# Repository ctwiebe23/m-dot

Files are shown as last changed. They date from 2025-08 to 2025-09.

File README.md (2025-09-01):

# Robot Car Project: M-DOT

Repo containing code and diagrams for a maze-navigating robot car built for my
Embedded Systems class.  The project uses an Arduino UNO, but operates purely
using the ATmega328P registers — no Arduino libraries.

## Directories

`./src`
: Contains C++ header and source files, as well as an executable program.  All
public function prototypes and macro definitions are in `mdot.hpp`, while all
implementations are split into their own `.cpp` files.  An example program
can be found in `src.ino`

`./doc`
: Contains documentation for the design of the project, such as wiring
diagrams and a report.

`./dat`
: Contains additional data, such as relevant datasheets and schematics.

## How to use M-DOT

M-DOT is a simple robot consisting of

- an Arduino UNO;
- an HC-SR04 ultrasonic sensor mounted on a servo;
- two DC motors connected to a L298N motor driver; and
- an IR receiver.

It can be controlled using the library found within this project, `mdot.hpp`.
This library consists of two types of functions:  Setup functions, and loop
functions.

The program entry point should be a `.ino` file that includes the M-DOT library
and contains a `setup()` function (ran once) along with a `loop()` function
(ran continuously).

```cpp
#include "mdot.hpp"

void setup(void) {
  configMDot();
  setDrift(0.95);
}

void loop(void) {
  Millimeters distance = getSonarDistance();

  if (distance < 40) {
    stop();
  } else {
    drive(100);
  }

  wait(100);
}
```

### Setup

The setup functions are intended to be used within the `setup()` Arduino
function.  They mostly follow the naming pattern `configFoo()` and are used to
configure each component, e.g. `configSonar()`, `configServo()`. For
convenience, a helper function `configMDot()` is provided that calls all other
configure functions.

Other setup functions include:

`void setDrift(float drift)`
: This function is used to handle drift in the drive (DC) motors.  It takes one
argument:  A float that represents the ratio of left motor power to right motor
power.  For instance, if M-DOT drifts to the right you might do:

```cpp
void setup(void) {
  configMDot();
  // M-DOT drifts right -> correct w/ motor ratio 90 : 100
  // 90 / 100 = 0.9
  setDrift(0.9);

  drive(100);
}

void loop(void) { }
```

### Main loop

The loop functions are intended to be used within the `loop()` Arduino
function, but are frequently used within `setup()` too.  They are what tells
M-DOT to execute various actions.  Most components only have one loop function.

`void curve(Percent leftPower, Percent rightPower)`
: Sets the speed and direction of each drive motor individually.

`void brake(void)`
: Brakes both motors, i.e. immediate stop.

`void drive(Percent power)`
: Expands to `curve(power, power)`.

`void pivot(Percent power)`
: Expands to `curve(power, -power)`.

`void stop(void)`
: Expands to `curve(0, 0)`.  Glide stop.

`void moveServoTo(Degrees angle)`
: Alters the servo angle.  Uses the range [-90, 90].

`Millimeters getSonarDistance(void)`
: Reads distance using the ultrasonic sensor.

`void wait(Milliseconds period)`
: Pause program execution.

`void startStopwatch(void)`
: Starts (or restarts) the stopwatch.

`Milliseconds getStopwatchTime(void)`
: Gets the current stopwatch time.

`ButtonPress getButtonPress(void)`
: Gets a button press from the IR receiver.

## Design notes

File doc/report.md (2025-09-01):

---
title: M-DOT
subtitle: Embedded Systems // Project Report
author: C Wiebe
date: May 9, 2025
numbersections: true
colorlinks: true
links-as-notes: true
toc: true
header:
  right: University of Placename
toc-on-own-page: true
margin-top: 1.2in
margin-bottom: 1.2in
margin-left: 1.2in
margin-right: 1.2in
fontfamily: tgschola
fontsize: 11pt
---

# Introduction

M-DOT is a Arduino-based maze-navigating robot car programmed using ATmega328P
registers and a custom library.  It uses two DC motors controlled by a L298
motor driver to maneuver, along with an HC-SR04 ultrasonic sensor mounted to a
SG90 servo to "see" its surroundings.  The goal of the project is to create a
robot car that can successfully navigate a maze-like obstacle course using its
onboard sensor.

Additionally, M-DOT can be controlled remotely using an AX-1838HS IR receiver
and Elegoo controller. This functionality is *not* used in maze navigation ---
that is totally autonomous.

# Preliminary Design

The robot has four main external components that need to be configured: The
servo, the sonar (ultrasonic sensor), the drivetrain (DC motors), and the (IR)
receiver.  They are
connected to the Arduino UNO as seen in Figure \ref{initial}

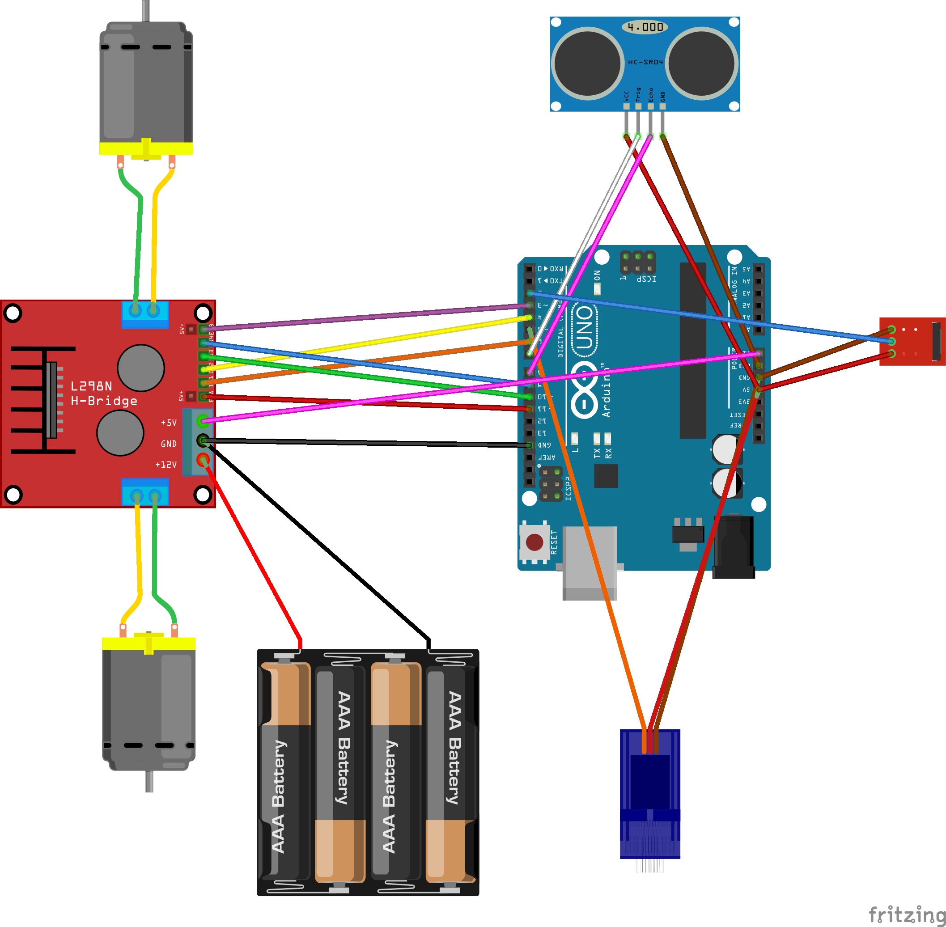
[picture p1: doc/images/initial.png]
Initial design schematic. \label{initial}


All three timers are used in configuring these components, as seen in Table
\ref{timers}.

: Timer configurations. \label{timers}

| Timer | Purpose | Mode | Output(s) |
| --- | --- | --- | --- |
| `timer0` | Servo PWM | Phase correct PWM | `OC0B` |
| `timer1` | General timer  | Normal | None |
| `timer2` | Drivetrain PWM | Phase correct PWM | `OC2A`, `OC2B` |

## Servo Configuration

In order to generate a PWM with the duty cycle and period expected by the SG90
servo, `timer0` was configured to use `OCR0A` as its TOP, the value of which
can be found with equation:
$$ \mathrm{TOP} = \mathrm{OCR0A} = \frac{\mathrm{CPU~frequency} \times
\mathrm{servo~period}}{\mathrm{prescaler} \times 2} = 156.25 \approx 156 $$
where:
\begin{alignat*}{3}
\mathrm{CPU~frequency} &= 16 \u{MHz} \\
\mathrm{servo~period} &= 20 \u{ms} \\
\mathrm{prescaler} &= 1024
\end{alignat*}

Since `OCR0A` is being used as TOP, the PWM is generated on `OC0B`.

## General Timer Configuration

General timer functions --- such as those needed by the sonar --- are provided
by `timer1`.  To this end, the timer is configured in normal mode with no major
modifications.  The timer does, however, make use of two interrupts:

1.  The timer overflow interrupt, `TOV1`, which will be used to increment a
    counter and track large spans of time.
2.  The output compare A interrupt, `OCIE1A`, which will be used by the
    receiver to determine when a data packet "times out".

## Sonar Configuration

The sonar uses two non-PWM pins --- one output (trigger) and one input (echo)
--- along with basic timer functions to measure signal lengths.

A reading begins by sending a ten microsecond pulse to the trigger.  The
duration of the return signal recieved on echo is then measured and used to
calculate the distance, using the equation:
$$ \mathrm{distance} \u{cm} = \mathrm{echo~duration}\u{\mu s} \times
\frac{\mathrm{centimeters}}{\mathrm{microsecond}} $$
where:
$$ \frac{\mathrm{centimeters}}{\mathrm{microsecond}} = 58 $$
Readings should be taken at least 60 milliseconds apart to prevent noise from
interfering with the measurement.

## Drivetrain Configuration

Each drivetrain motor is hooked into the L298 motor driver with two pins. The
Arduino itself is connected to the L298 using a three-wire interface (three
pins per motor):

- One wire is a PWM that connects to the motor enable pin and controls the
  "power" of the motor.
- The other two (non-PWM) wires control the direction of the motor.  When one
  pin is HIGH and the other LOW, the motor spins one way; swap which pin is
  HIGH and which is LOW to spin the motor the other way.  Set both pins equal
  to each other to "brake" the motor.

`timer2` is used to generate the PWM signals needed for both motor enable
wires.  These are generated on pins `OC2A` and `OC2B`.

## Receiver Configuration

The IR receiver will be hooked up to an external interrupt (which is idle HIGH)
so as to prevent the need for constant polling.  It will use `timer1` as a
pseudo watchdog timer by enabling and disabling an output compare match
interrupt.

The following process is used to receive data, which it stores in a
global "data packet":

1.  The external interrupt ISR is configured to fire on the falling edge,
    but that trigger will toggle between falling and rising edges each time it
    is called.
2.  When a falling edge interrupt fires, the current timer count is stored in
    the data packet and the watchdog timer is disabled, if it isn't already.
3.  When the rising edge interrupt fires, the timer count is cleared and the
    watchdog timer is started.  If the watchdog timer terminates, the data
    packet is marked as complete and the process is reset.

Each data packet sent will begin with a start bit, followed by 32 data bits,
and terminating with an end bit.  Each bit will consist of a "low half-bit" and
a "high half-bit".  The low half of the data bits is used to separate the high
halves, which will contain the actual data:  A long time spent high is a
logical 1, and a short time high is a logical 0.  The time spent low is
funtionally irrevelent.  Recorded times for the various half-bits can be seen
in Table \ref{lengths}.

: Recorded half-bit lengths.
\label{lengths}

| Type | Time [ms] |
| --- | ---: |
| Start low | 9.336 |
| Start high  | 4.456 |
| Data X low  | 0.644 |
| Data 0 high | 0.504 |
| Data 1 high | 1.592 |
| Stop low | 0.656 |
| Stop high | 39.992 |

In order to properly identify 1's and 0's in the data segement, additional
analysis was conducted, as seen in Table \ref{stats}.  The valid range
displayed in the table is the range that will correctly identify 99.9999426697%
of pulses (plus or minus five standard deviations).

: Average, standard deviation, and valid ranges for data half-bits.
\label{stats}

| Type | Avg [ms] | Stdev [$\mu$s] | Range [ms] |
| --- | ---: | ---: | ---: |
| Data X low  | 0.661 | 16.60 | 0.578 to 0.744 |
| Data 0 high | 0.506 | 2.14 | 0.495 to 0.517 |
| Data 1 high | 1.592 | 9.90 | 1.542 to 1.641 |

With that, various buttons on the Elegoo IR controller were mapped to their
corresponding hex codes, and can be seen in Table \ref{buttons}.

: Recognized buttons.
\label{buttons}

| Button | Hex code |
| --- | ---: |
| `POWER` | `0x00FFA25D` |
| `VOL+` | `0x00FF629D` |
| `FUNC/STOP` | `0x00FFE21D` |
| `FAST BACK` | `0x00FF22DD` |
| `PAUSE` | `0x00FF02FD` |
| `FAST FORWARD` | `0x00FFC23D` |
| `DOWN` | `0x00FFE01F` |
| `VOL-` | `0x00FFA857` |
| `UP` | `0x00FF906F` |
| `EQ` | `0x00FF9867` |

# Software Implementation

M-DOT is programmed with a conceptually simple algorithm --- Algorithm
\ref{main} --- which navigates by taking sonar measurements while stationary
and moving in discrete bursts based on those measurements.  The four "cases"
for how it moves are:

1.  *If an object is in the immediate drive path,* pivot 90 degrees away from
    the wall.
2.  *Else if the wall is too close,* curve away from it.
3.  *Else if the wall is very far (twice the ideal distance),* curve sharply
    towards the wall.
4.  *Else,* curve towards the wall.

The algorithm is designed so that there is not a hard-coded "target distance"
from the wall that M-DOT tries to reach --- rather, the robot will measure its
initial distance from the wall on start-up and then try and maintain that
distance throughout its travels.

\begin{algorithm}
\caption{M-DOT's primary process. \label{main}}
\Fn{$\alfn{Navigate}$}{
  $idealDistance \gets \mathrm{measure~distance~to~wall}$\;
  \While{$true$}{
    $wallMargin \gets \textsc{CheckWall}(idealDistance)$\;
    $frontMargin \gets \textsc{CheckFront}(idealDistance)$\;
    \uIf{$frontMargin < 0$}{
      $\mathrm{pivot~90~degrees~from~wall}$\;
    }\uElseIf{$wallMargin < 0$}{
      $\mathrm{curve~away~from~wall}$\;
    }\uElseIf{$wallMargin > idealDistance$}{
      $\mathrm{curve~sharply~towards~wall}$\;
    }\Else{
      $\mathrm{curve~towards~wall}$\;
    }
    $\mathrm{brake~the~robot}$\;
  }
}
\end{algorithm}

$\textsc{CheckWall}$ and $\textsc{CheckFront}$ (Algorithms \ref{wall} and
\ref{front}) are two near-identical processes that simply return the difference
between the ideal distance and the current following distance, as measured from
both the side and the front.

\begin{algorithm}
\caption{Measures the distance to the wall. \label{wall}}
\Fn{$\alfn{CheckWall}(idealDistance)$}{
  $currentDistance \gets \mathrm{measure~distance~to~wall}$\;
  \Return{$currentDistance - idealDistance$}
}
\end{algorithm}

\begin{algorithm}
\caption{Measures the distance to the nearest obstacle. \label{front}}
\Fn{$\alfn{CheckFront}(idealDistance)$}{
  $currentDistance \gets \mathrm{measure~distance~to~front}$\;
  \Return{$currentDistance - idealDistance$}
}
\end{algorithm}

M-DOT also features a much faster wall-following algorithm, Algorithm
\ref{algo}, that is an alternative to $\textsc{Navigate}$ as a program "entry
point".  This method does not account for obstacles in the drive path, but
neither does it constantly start and stop.

\begin{algorithm}
\caption{A simple wall-following algorithm for M-DOT. \label{algo}}
\Fn{$\alfn{FollowWall}$}{
  $idealDistance \gets \mathrm{measure~the~distance~to~the~wall}$\;
  $tolerance \gets \mathrm{acceptable~margin~of~error}$\;
  \While{$true$}{
    $currentDistance \gets \mathrm{measure~the~distance~to~the~wall}$\;
    \uIf{$currentDistance > idealDistance + tolerance$}{
      drive curving towards the wall\;
    }\uElseIf{$currentDistance < idealDistance - tolerance$}{
      drive curving away from the wall\;
    }\Else{
      drive straight ahead\;
    }
  }
}
\end{algorithm}

# Hardware Implementation

M-DOT is constructed in accordance with the initial design schematic seen in
Figure \ref{initial} (which is also the final hardware schematic), with the pin
assignments seen in Table \ref{pins}.

: Pin assignments. \label{pins}

| Component | Arduino Pin | ATmega328P Pin | Special Function |
| --- | ---: | ---: | --- |
| Servo control  | 5 | `PD5` | `OC0B` |
| Sonar trigger  | 7 | `PD7` | |
| Sonar echo | 8 | `PB0` | |
| Motor A enable | 11 | `PB3` | `OC2A` |
| Motor A + | 6 | `PD6` | |
| Motor A -- | 4 | `PD4` | |
| Motor B enable | 3 | `PD3` | `OC2B` |
| Motor B + | 10 | `PB2` | |
| Motor B -- | 9 | `PB1` | |
| Error report | 13 | `PB5` | Built-in LED |
| IR signal | 2 | `PD2` | `INT0` |

The sonar should be angled on its servo so that it is always facing a surface
head-on.  This is because the wave sent out by the sonar needs to bounce of the
surface and return --- if the surface is at an angle away from the sonar, the
wave can bounce away and never return, as seen in Figure \ref{bounce}.

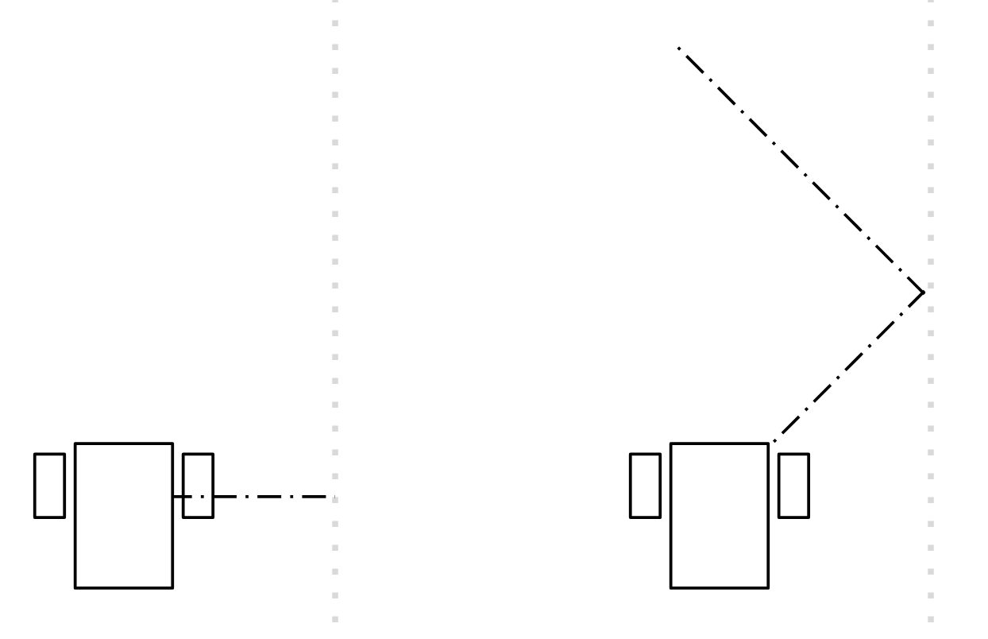
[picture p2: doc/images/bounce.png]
If the sonar is at too large an angle with the surface it is facing, the return signal could bounce away. \label{bounce}
{
width=70% }

However, if the sonar is measuring along M-DOT's center of rotation then it may
not detect the robot drifting off-course quick enough to prevent that angle
from growing dangerous, as seen in Figure \ref{axis}.

To this end, the sonar is kept at a 30 degree offset from the wall, as seen in
Figure \ref{offset} --- large enough to detect alterations to M-DOT's drive
path early, but small enough to still receive a return wave that can measured
with confidence.

\begin{figure}[!tbp]
  \centering
  \begin{minipage}[t]{0.45\textwidth}
    \includegraphics[width=\textwidth]{./images/axis.png}
    \caption{The measured distance does not differ much between the two points
    when measuring along the center of rotation.}
    \label{axis}
  \end{minipage}
  \hfill
  \begin{minipage}[t]{0.45\textwidth}
    \includegraphics[width=\textwidth]{./images/offset.png}
    \caption{There is a much more noticeable difference between the measured
    distances when measuring at an offset.}
    \label{offset}
  \end{minipage}
\end{figure}

# Testing

## Debugging

There were a few issues encountered during the testing process that had to be
debugged, all of which concerned the sonar.  First and foremost among them was
the fact that the sonar could not get a reading from an angled surface, which
was not considered during the preliminary design and had to be adjusted for
when implementing and testing the project.

The other major hiccup was that the `getSonarDistance()` function (initially)
did not force the 60 millisecond measurement cycle itself, so it was easy to
forget and try to take back-to-back measurements.

Both of these issues where debugged by simply taking measurements with the
sonar and printing them to the serial monitor in a loop while observing the
output.

---

Other design challenges that were encountered (but that are not considered
"bugs" per se) include:

- A relatively slow angular velocity on the servo, which forced ~500
  millisecond measurement cycles when watching both the front and the side ---
  200ms per turn and 60ms per sonar reading.  This made moving while measuring
  dangerous at any appreciable speed in the full navigation algorithm.
- Inaccurate sonar measurements while moving, which further encouraged using
  the sonar while stationary.
- Drivetrain drift that varied based on how hot the motors are, which
  discouraged using precise powers to drive the motors.

## Testing Methodology

Testing of M-DOT happened in multiple stages:

1.  Each component was tested individually to confirm basic functionality, e.g.
    checking to make sure the servo spins and the sonar returns an accurate
    distance.
2.  The drivetrain was tested for drift by driving it straight forward at max
    speed and observing its path.
3.  The range of angles at which the sonar can get a valid reading was measured
    by taking readings at increasing angles until the output became unreliable.
4.  The full program was then tested in various environments (carpeted floors
    vs. smooth floors, varying initial distances from the wall, etc.).

## Results

Each component was able to perform its basic functionality without trouble,
though the drivetrain as a whole did drift to the right by a not insignificant
amount.  This was corrected for in the code by reducing the power sent to the
left motor by five percent at all times.  The sonar was found to be able to
take accurate measurements up to around a 30 degree offset from the opposite
surface, at which point the measurements became unusable.

M-DOT then completed several tests verifying the functionality of its
navigation algorithms, such as [following a
wall](https://www.youtube.com/watch?v=LuJOR8e18cY) with the simplified
algorithm and [navigating a small
course](https://www.youtube.com/watch?v=sb-tt6APl8w) with the full algorithm.

# Q&A

## Motor Driver

How are the motors wired up?  Is it a two or three wire interface?
: The motors themselves are hooked into the L298 motor driver with two pins
each. The Arduino is connected to the L298 using a three-wire interface (three
pins per motor): one PWM pin specifying speed, and two pins controlling
direction.

What will be done with the motor enable pins?
: The motor enable pins are connected to PWM signals and used to control the
speed of the motors.

What pins/timer will create the PWM signals?
: The PWM signals will be generated on pins `OC2A` (Pin 11) and `OC2B` (Pin 3)
using `timer2`.

How will the motors change direction?
: The direction of the motors will be controlled by the non-PWM pins in the
three-wire interface --- when one pin is HIGH and the other LOW, the motors
spin forward; swap which pin is HIGH and which is LOW to spin backwards.

## IR Receiver

How long does `timer1` take to roll over?
: Overflows take 262.14 milliseconds in my implementation.

How long does a timer count last with a prescaler of 64?
: Given the CPU frequency of 16 megahertz on the Arduino UNO, each count will
last four microseconds.

How long are the pulses generated by the IR remote?
: Pulse lengths can be seen in Table \ref{lengths}.

What is the average/standard deviation of each pulse type?
: Statistical analysis on pulse lengths can be seen in Table \ref{stats}.

What are the hex codes for the buttons on the IR remote?
: Button codes can be seen in Table \ref{buttons}.

# Conclusion

The drivetrain, servo, sonar, and receiver were all successfully configured to
maneuver M-DOT and take accurate distance measurements --- without using the
Arduino library. With these components, the robot was able to demonstrate
wall-following and maze-navigation capabilities, culminating in two runs
demonstrating full navigation:  One with [smoother, safer, and slower
defaults](https://www.youtube.com/watch?v=uleEuvvNTLQ), and one with [a little
more speed and a little more
sway](https://www.youtube.com/watch?v=FaIQ-QEpM34).

# Documentation

No collaboration.

Resources used:

- Various datasheets for the ATmega328P, HC-SR04, L298, SG90, and AX-1883HS.
- Schematic for the Arduino UNO.
- [Fritzing](https://fritzing.org) for wiring diagrams.
- Class resources such as slides and recorded videos.

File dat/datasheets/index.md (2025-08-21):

# ATmega328P

## timer1

20.14.1 `TCCR1A`
: `COM`, `WGM`, Modes

20.14.2 `TCCR1B`
: `CS` bits, Prescalers, `WGM`, Input capture noise

20.14.12 `TIMSK1`
: Interrupt masks

20.14.12 `TIFR1`
: Interrupt flags

## timer2

22.11.1 `TCCR2A`
: `COM`, `WGM`, Modes

22.11.2 `TCCR2B`
: `CS` bits, Prescalers, `WGM`

## Interrupts

11.7. Interrupts
: General

16.1. Interrupt vectors
: Vector table

17.2. External interrupts
: `EICRA`

## UART

24.4.1 Baud rates
: BAUD and `UBRRn` values

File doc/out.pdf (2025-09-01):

## M-DOT

Embedded Systems // Project Report

C Wiebe

May 9, 2025

## Contents

1 Introduction | 3
2 Preliminary Design | 3
3 Software Implementation | 6
4 Hardware Implementation | 8
5 Testing | 9
6 Q&A | 11
7 Conclusion | 12
8 Documentation | 12

University of Placename

## 1 Introduction

M-DOT is a Arduino-based maze-navigating robot car programmed using ATmega328P registers and a custom library. It uses two DC motors controlled by a L298 motor driver to maneuver, along with an HC-SR04 ultrasonic sensor mounted to a SG90 servo to “see” its surroundings. The goal of the project is to create a robot car that can successfully navigate a maze-like obstacle course using its onboard sensor.

Additionally, M-DOT can be controlled remotely using an AX-1838HS IR receiver and Elegoo controller. This functionality is not used in maze navigation — that is totally autonomous.

## 2 Preliminary Design

The robot has four main external components that need to be configured: The servo, the sonar (ultrasonic sensor), the drivetrain (DC motors), and the (IR) receiver. They are connected to the Arduino UNO as seen in Figure 1


Figure 1: Initial design schematic.

All three timers are used in configuring these components, as seen in Table 1.

Table 1: Timer configurations.

Timer | Purpose | Mode | Output(s)
timer0 | Servo PWM | Phase correct PWM OC0B
timer1 | General timer | Normal | None
timer2 | Drivetrain PWM Phase correct PWM OC2A, OC2B

### 2.1 Servo Configuration

In order to generate a PWM with the duty cycle and period expected by the SG90 servo, timer0 was configured to use OCR0A as its TOP, the value of which can be found with equation:

TOP = OCR0A = CPU frequency × servo period prescaler × 2

= 156.25 ≈ 156

where:

CPU frequency = 16 [MHz]
servo period = 20 [ms]

prescaler = 1024

Since OCR0A is being used as TOP, the PWM is generated on OC0B.

### 2.2 General Timer Configuration

General timer functions — such as those needed by the sonar — are provided by timer1. To this end, the timer is configured in normal mode with no major modifications. The timer does, however, make use of two interrupts:

1. The timer overflow interrupt, TOV1, which will be used to increment a counter and track large spans of time.
2. The output compare A interrupt, OCIE1A, which will be used by the receiver to determine when a data packet “times out”.

### 2.3 Sonar Configuration

The sonar uses two non-PWM pins — one output (trigger) and one input (echo) — along with basic timer functions to measure signal lengths.

A reading begins by sending a ten microsecond pulse to the trigger. The duration of the return signal recieved on echo is then measured and used to calculate the distance, using the equation:

distance [cm] = echo duration [µs] ×

centimeters
microsecond
where:
centimeters
microsecond = 58

Readings should be taken at least 60 milliseconds apart to prevent noise from interfering with the measurement.

### 2.4 Drivetrain Configuration

Each drivetrain motor is hooked into the L298 motor driver with two pins. The Arduino itself is connected to the L298 using a three-wire interface (three pins per motor):

- One wire is a PWM that connects to the motor enable pin and controls the “power” of the motor.
- The other two (non-PWM) wires control the direction of the motor. When one pin is HIGH and the other LOW, the motor spins one way; swap which pin is HIGH and which is LOW to spin the motor the other way. Set both pins equal to each other to “brake” the motor.

timer2 is used to generate the PWM signals needed for both motor enable wires. These are generated on pins OC2A and OC2B.

### 2.5 Receiver Configuration

The IR receiver will be hooked up to an external interrupt (which is idle HIGH) so as to prevent the need for constant polling. It will use timer1 as a pseudo watchdog timer by enabling and disabling an output compare match interrupt.

The following process is used to receive data, which it stores in a global “data packet”:

1. The external interrupt ISR is configured to fire on the falling edge, but that trigger will toggle between falling and rising edges each time it is called.
2. When a falling edge interrupt fires, the current timer count is stored in the data packet and the watchdog timer is disabled, if it isn’t already.
3. When the rising edge interrupt fires, the timer count is cleared and the watchdog timer is started. If the watchdog timer terminates, the data packet is marked as complete and the process is reset.

Each data packet sent will begin with a start bit, followed by 32 data bits, and terminating with an end bit. Each bit will consist of a “low half-bit” and a “high half-bit”. The low half of the data bits is used to separate the high halves, which will contain the actual data: A long time spent high is a logical 1, and a short time high is a logical 0. The time spent low is funtionally irrevelent. Recorded times for the various half-bits can be seen in Table 2.

Table 2: Recorded half-bit lengths.

Type | Time [ms]
Start low | 9.336
Start high | 4.456
Data X low | 0.644
Data 0 high | 0.504
Data 1 high | 1.592
Stop low | 0.656
Stop high | 39.992

In order to properly identify 1’s and 0’s in the data segement, additional analysis was conducted, as seen in Table 3. The valid range displayed in the table is the range that will correctly identify 99.9999426697% of pulses (plus or minus five standard deviations).

Table 3: Average, standard deviation, and valid ranges for data half-bits.

Type | Avg [ms] Stdev [µs] | Range [ms]
Data X low | 0.661 | 16.60 0.578 to 0.744
Data 0 high | 0.506 | 2.14 0.495 to 0.517
Data 1 high | 1.592 | 9.90 | 1.542 to 1.641

With that, various buttons on the Elegoo IR controller were mapped to their corresponding hex codes, and can be seen in Table 4.

Table 4: Recognized buttons.

Button | Hex code
POWER | 0x00FFA25D
VOL+ | 0x00FF629D
FUNC/STOP | 0x00FFE21D
FAST BACK | 0x00FF22DD
PAUSE | 0x00FF02FD
FAST FORWARD | 0x00FFC23D
DOWN | 0x00FFE01F
VOL- | 0x00FFA857
UP | 0x00FF906F
EQ | 0x00FF9867

## 3 Software Implementation

M-DOT is programmed with a conceptually simple algorithm — Algorithm 1 — which navigates by taking sonar measurements while stationary and moving in discrete bursts based on those measurements. The four “cases” for how it moves are:

1. If an object is in the immediate drive path, pivot 90 degrees away from the wall.
2. Else if the wall is too close, curve away from it.
3. Else if the wall is very far (twice the ideal distance), curve sharply towards the wall.
4. Else, curve towards the wall.

The algorithm is designed so that there is not a hard-coded “target distance” from the wall that M-DOT tries to reach — rather, the robot will measure its initial distance from the wall on start-up and then try and maintain that distance throughout its travels.

CheckWall and CheckFront (Algorithms 2 and 3) are two near-identical processes that simply return the difference between the ideal distance and the current following distance, as measured from both the side and the front.

Algorithm 1: M-DOT’s primary process.

### 1 function Navigate is

### 2 idealDistance ← measure distance to wall

### 3 while true do

### 4 wallM argin ← CheckWall(idealDistance) 5 frontM argin ← CheckFront(idealDistance) 6 if frontM argin < 0 then 7 pivot 90 degrees from wall 8 else if wallM argin < 0 then 9 curve away from wall 10 else if wallM argin > idealDistance then 11 curve sharply towards wall

### 12 else

### 13 curve towards wall

### 14 brake the robot

Algorithm 2: Measures the distance to the wall.

### 1 function CheckWall(idealDistance) is 2 currentDistance ← measure distance to wall 3 return currentDistance − idealDistance

Algorithm 3: Measures the distance to the nearest obstacle.

### 1 function CheckFront(idealDistance) is 2 currentDistance ← measure distance to front 3 return currentDistance − idealDistance

M-DOT also features a much faster wall-following algorithm, Algorithm 4, that is an alternative to Navigate as a program “entry point”. This method does not account for obstacles in the drive path, but neither does it constantly start and stop.

Algorithm 4: A simple wall-following algorithm for M-DOT.

### 1 function FollowWall is

### 2 idealDistance ← measure the distance to the wall 3 tolerance ← acceptable margin of error

### 4 while true do

### 5 currentDistance ← measure the distance to the wall 6 if currentDistance > idealDistance + tolerance then

### 7 drive curving towards the wall

### 8 else if currentDistance < idealDistance − tolerance then

### 9 drive curving away from the wall 10 else 11 drive straight ahead

## 4 Hardware Implementation

M-DOT is constructed in accordance with the initial design schematic seen in Figure 1 (which is also the final hardware schematic), with the pin assignments seen in Table 5.

Table 5: Pin assignments.

Component | Arduino Pin ATmega328P Pin Special Function
Servo control | 5 | PD5 | OC0B
Sonar trigger | 7 | PD7
Sonar echo | 8 | PB0
Motor A enable | 11 | PB3 | OC2A
Motor A + | 6 | PD6
Motor A – | 4 | PD4
Motor B enable | 3 | PD3 | OC2B
Motor B + | 10 | PB2
Motor B – | 9 | PB1
Error report | 13 | PB5 | Built-in LED
IR signal | 2 | PD2 | INT0

The sonar should be angled on its servo so that it is always facing a surface head-on. This is because the wave sent out by the sonar needs to bounce of the surface and return — if the surface is at an angle away from the sonar, the wave can bounce away and never return, as seen in Figure 2.


Figure 2: If the sonar is at too large an angle with the surface it is facing, the return signal could bounce away.

However, if the sonar is measuring along M-DOT’s center of rotation then it may not detect the robot drifting off-course quick enough to prevent that angle from growing dangerous, as seen in Figure 3.

To this end, the sonar is kept at a 30 degree offset from the wall, as seen in Figure 4 — large enough to detect alterations to M-DOT’s drive path early, but small enough to still receive a return wave that can measured with confidence.

## 5 Testing

### 5.1 Debugging

There were a few issues encountered during the testing process that had to be debugged, all of which concerned the sonar. First and foremost among them was the fact that the sonar could not get a reading from an angled surface, which was not considered during the preliminary design and had to be adjusted for when implementing and testing the project.

The other major hiccup was that the getSonarDistance() function (initially) did not force the 60 millisecond measurement cycle itself, so it was easy to forget and try to take back-to-back measurements.

Both of these issues where debugged by simply taking measurements with the sonar and printing them to the serial monitor in a loop while observing the output.

Other design challenges that were encountered (but that are not considered “bugs” per se) include:

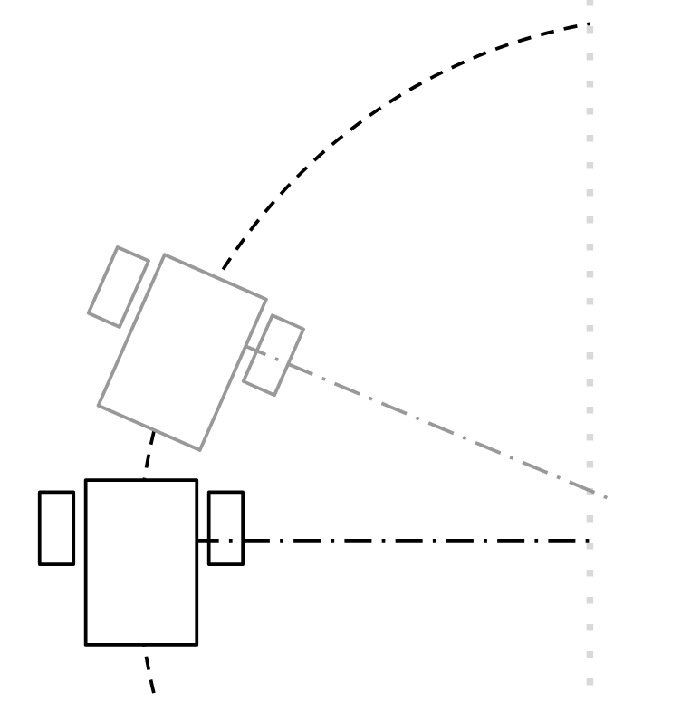
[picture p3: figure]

Figure 3: The measured distance does not differ much between the two points when measuring along the center of rotation.

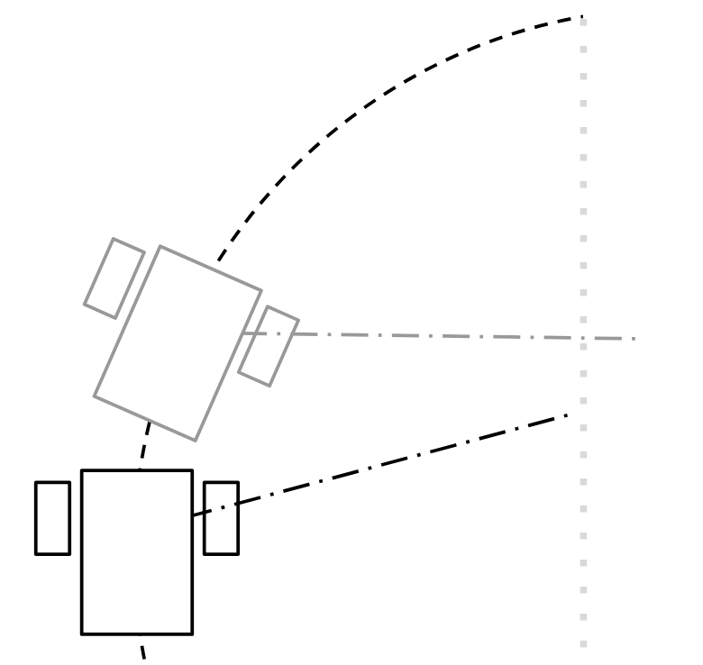
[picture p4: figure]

Figure 4: There is a much more noticeable difference between the measured distances when measuring at an offset.

- A relatively slow angular velocity on the servo, which forced ~500 millisecond measurement cycles when watching both the front and the side — 200ms per turn and 60ms per sonar reading. This made moving while measuring dangerous at any appreciable speed in the full navigation algorithm.
- Inaccurate sonar measurements while moving, which further encouraged using the sonar while stationary.
- Drivetrain drift that varied based on how hot the motors are, which discouraged using precise powers to drive the motors.

### 5.2 Testing Methodology

Testing of M-DOT happened in multiple stages:

1. Each component was tested individually to confirm basic functionality, e.g. checking to make sure the servo spins and the sonar returns an accurate distance.
2. The drivetrain was tested for drift by driving it straight forward at max speed and observing its path.
3. The range of angles at which the sonar can get a valid reading was measured by taking readings at increasing angles until the output became unreliable.
4. The full program was then tested in various environments (carpeted floors vs. smooth floors, varying initial distances from the wall, etc.).

### 5.3 Results

Each component was able to perform its basic functionality without trouble, though the drivetrain as a whole did drift to the right by a not insignificant amount. This was corrected for in the code by reducing the power sent to the left motor by five percent at all times. The sonar was found to be able to take accurate measurements up to around a 30 degree offset from the opposite surface, at which point the measurements became unusable.

M-DOT then completed several tests verifying the functionality of its navigation algorithms, such as following a wall¹ with the simplified algorithm and navigating a small course² with the full algorithm.

## 6 Q&A

### 6.1 Motor Driver

How are the motors wired up? Is it a two or three wire interface? The motors themselves are hooked into the L298 motor driver with two pins each. The Arduino is connected to the L298 using a three-wire interface (three pins per motor): one PWM pin specifying speed, and two pins controlling direction.
What will be done with the motor enable pins? The motor enable pins are connected to PWM signals and used to control the speed of the motors.
What pins/timer will create the PWM signals? The PWM signals will be generated on pins OC2A (Pin 11) and OC2B (Pin 3) using timer2.
How will the motors change direction? The direction of the motors will be controlled by the non-PWM pins in the three-wire interface — when one pin is HIGH and the other LOW, the motors spin forward; swap which pin is HIGH and which is LOW to spin backwards.

### 6.2 IR Receiver

How long does timer1 take to roll over? Overflows take 262.14 milliseconds in my implementation.
How long does a timer count last with a prescaler of 64? Given the CPU frequency of 16 megahertz on the Arduino UNO, each count will last four microseconds. How long are the pulses generated by the IR remote? Pulse lengths can be seen in Table 2.
What is the average/standard deviation of each pulse type? Statistical analysis on pulse lengths can be seen in Table 3.
What are the hex codes for the buttons on the IR remote? Button codes can be seen in Table 4.

1https://www.youtube.com/watch?v=LuJOR8e18cY2https://www.youtube.com/watch?v=sb-tt6APl8w

## 7 Conclusion

The drivetrain, servo, sonar, and receiver were all successfully configured to maneuver M-DOT and take accurate distance measurements — without using the Arduino library. With these components, the robot was able to demonstrate wall-following and mazenavigation capabilities, culminating in two runs demonstrating full navigation: One with smoother, safer, and slower defaults³
, and one with a little more speed and a little more sway⁴

## 8 Documentation

No collaboration.

Resources used:

- Various datasheets for the ATmega328P, HC-SR04, L298, SG90, and AX-1883HS.
- Schematic for the Arduino UNO.
- Fritzing⁵
for wiring diagrams.
- Class resources such as slides and recorded videos.

3https://www.youtube.com/watch?v=uleEuvvNTLQ4https://www.youtube.com/watch?v=FaIQ-QEpM345https://fritzing.org

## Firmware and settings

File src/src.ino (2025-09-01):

/**
 * @author  C Wiebe
 * @date    2025-04-22
 * @course  Embedded Systems (Spring 2025)
 * @file    src.ino
 * @hw      Project 2
 * @brief   Entry point for a program that uses M-DOT.
 * @doc     No collaboration.
 *
 * Academic Integrity Statement:  I certify that, while others may have
 * assisted me in brain storming, debugging and validating this program, the
 * program itself is my own work.  I understand that submitting code which is
 * the work of other individuals is a violation of the honor code.  I also
 * understand that if I knowingly give my original work to another individual
 * is also a violation of the honor code.
 */

#include "mdot.hpp"

#define SERVO_MS    120  // Time it takes to pivot the servo
#define JAUNT_MS    200  // Time alloted for each "step"
#define WALL_ANGLE  -60  // Angle at which to measure the wall
#define FRONT_ANGLE -30  // Angle at which to measure the front

Millimeters ideal = -1;  // The initial distance to the wall at startup

void setup(void)
{
    configMDot();
    wait(500);  // Wait for everything to set up; sonar breaks otherwise

    RUN(moveServoTo(WALL_ANGLE), 250);
    ideal = getSonarDistance();
    wait(250);
}

Millimeters checkWall(void)
{
    RUN(moveServoTo(WALL_ANGLE), SERVO_MS);
    Millimeters wall = getSonarDistance();

    return wall - ideal;
}

Millimeters checkFront(void)
{
    RUN(moveServoTo(FRONT_ANGLE), SERVO_MS);
    Millimeters front = getSonarDistance();

    return front - ideal;
}

void loop(void)
{
    Millimeters frontMargin = checkFront();
    Millimeters wallMargin = checkWall();

    if (frontMargin < 0)
        pivot(-50);  // Immediate obstacle in path; panic!
    else if (wallMargin < 0)
        curve(30, 80);  // Too close to wall; move outwards
    else if (wallMargin > ideal)
        curve(80, 30);  // *Very* far from wall; move inwards at sharp angle
    else
        curve(70, 50);  // Too far from wall; move inwards

    wait(JAUNT_MS);
    brake();
}

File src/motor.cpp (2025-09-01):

/**
 * @author  C Wiebe
 * @date    2025-03-31
 * @course  Embedded Systems (Spring 2025)
 * @file    motor.cpp
 * @hw      Project 1
 * @brief   Implementation file containing code for the motors.
 * @doc     No collaboration.
 *
 * Academic Integrity Statement:  I certify that, while others may have
 * assisted me in brain storming, debugging and validating this program, the
 * program itself is my own work.  I understand that submitting code which is
 * the work of other individuals is a violation of the honor code.  I also
 * understand that if I knowingly give my original work to another individual
 * is also a violation of the honor code.
 */

#include "mdot.hpp"

/**
 * Configures all motor pins as outputs for the given motor.
 * @note The motor *must* have properly named pin macros.
 * @param NAME The name of the motor.
 */
#define CONFIG_MOTOR(NAME)                                                    \
    DDRx_##NAME##_ENABLE |= BIT_##NAME##_ENABLE;                              \
    DDRx_##NAME##_POSITIVE |= BIT_##NAME##_POSITIVE;                          \
    DDRx_##NAME##_NEGATIVE |= BIT_##NAME##_NEGATIVE;

/**
 * The modifiers [-1, 1] used to alter all motor powers.  Each power is
 * multiplied by its modifier, so a modifier of 1 results in no change.
 */
static float leftModifier = 1, rightModifier = 1;

void configMotors(void)
{
    CONFIG_MOTOR(A);
    CONFIG_MOTOR(B);

    // Phase correct PWM; OC2A and OC2B are outputs
    TCCR2A = (1 << WGM20) | (1 << COM2A1) | (1 << COM2B1);
    TCCR2B = (1 << CS22);  // Prescaler = 256

    leftModifier = rightModifier = 1;  // Both motors drive at 100% power

    TCNT2 = 0;  // Clear timer
    stop();     // Halt M-DOT
}

void setDrift(float drift)
{
    int8_t sign = 1;

    if (drift < 0) {
        sign = -1;
        drift *= -1;
    }

    if (drift < 1) {
        leftModifier = drift * sign;
        rightModifier = sign;
    } else {
        leftModifier = sign;
        rightModifier = 1 / drift * sign;
    }
}

/**
 * Converts power to counts (takes the absolute value of the power).
 * @param power The power.
 * @return The number of counts.
 */
static OutputCompareUnits powerToCounts(Percent power)
{
    if (power < 0)
        power *= -1;

    // counts = power / 100 * max counts
    return (OutputCompareUnits)((float)power * 2.55);
}

/**
 * Alters motor direction based on the sign of the motor power.
 * @note The motor *must* have properly named pin macros.
 * @param NAME The name of the motor.
 * @param POWER The new power.
 */
#define CHANGE_MOTOR_DIRECTION(NAME, POWER)                                   \
    if (POWER > 0) {                                                          \
        PORTx_##NAME##_POSITIVE |= BIT_##NAME##_POSITIVE;                     \
        PORTx_##NAME##_NEGATIVE &= ~BIT_##NAME##_NEGATIVE;                    \
    } else if (POWER < 0) {                                                   \
        PORTx_##NAME##_POSITIVE &= ~BIT_##NAME##_POSITIVE;                    \
        PORTx_##NAME##_NEGATIVE |= BIT_##NAME##_NEGATIVE;                     \
    } else {                                                                  \
        PORTx_##NAME##_POSITIVE |= BIT_##NAME##_POSITIVE;                     \
        PORTx_##NAME##_NEGATIVE |= BIT_##NAME##_NEGATIVE;                     \
    }

/**
 * Brakes the motor.  The motor must be enabled for the braking to take effect.
 * @note The motor *must* have properly named pin macros.
 * @param NAME The name of the motor.
 */
#define BRAKE_MOTOR(NAME)                                                     \
    PORTx_##NAME##_POSITIVE |= BIT_##NAME##_POSITIVE;                         \
    PORTx_##NAME##_NEGATIVE |= BIT_##NAME##_NEGATIVE;

void curve(Percent powerLeft, Percent powerRight)
{
    powerLeft *= leftModifier;
    powerRight *= rightModifier;

    // Alter "speed" of motor
    OCR2A = powerToCounts(powerLeft);
    OCR2B = powerToCounts(powerRight);

    // Alter direction of motor
    CHANGE_MOTOR_DIRECTION(A, powerLeft);
    CHANGE_MOTOR_DIRECTION(B, powerRight);
}

void brake(void)
{
    BRAKE_MOTOR(A);
    BRAKE_MOTOR(B);

    OCR2A = powerToCounts(100);
    OCR2B = powerToCounts(100);

    wait(50);
}

void drive(Percent power) { curve(power, power); }

void pivot(Percent power) { curve(power, -power); }

void stop(void) { curve(0, 0); }

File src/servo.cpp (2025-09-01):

/**
 * @author  C Wiebe
 * @date    2025-03-31
 * @course  Embedded Systems (Spring 2025)
 * @file    servo.cpp
 * @hw      Project 1
 * @brief   Implementation file containing code for the servo.
 * @doc     No collaboration.
 *
 * Academic Integrity Statement:  I certify that, while others may have
 * assisted me in brain storming, debugging and validating this program, the
 * program itself is my own work.  I understand that submitting code which is
 * the work of other individuals is a violation of the honor code.  I also
 * understand that if I knowingly give my original work to another individual
 * is also a violation of the honor code.
 */

#include "mdot.hpp"

// TOP = cpu frequency / prescaler / servo frequency / 2
#define TOP 156  // actual TOP = 156.25

void configServo(void)
{
    DDRx_SERVO |= BIT_SERVO;

    // Phase correct PWM; OC0B is output
    TCCR0A = (1 << WGM00) | (1 << COM0B1);

    // TOP = OCR0A; Prescaler = 1024
    TCCR0B = (1 << WGM02) | (1 << CS02) | (1 << CS00);

    OCR0A = TOP;     // Defines the overflow period
    TCNT0 = 0;       // Clear timer
    moveServoTo(0);  // Center position
}

void moveServoTo(Degrees angle)
{
    // ideal duty cycle = (angle / 180 + 1.5) / period (ms) * TOP
    // actual duty cycle = (angle / 90 + 1.5) / period (ms) * TOP
    float dutyCycle = ((float)angle / 11.52) + 11.71875;

    if (dutyCycle < 4)
        dutyCycle = 4;  // Absolute minimum value
    else if (dutyCycle > 19)
        dutyCycle = 19;  // Absolute maximum value

    OCR0B = (OutputCompareUnits)dutyCycle;
}
